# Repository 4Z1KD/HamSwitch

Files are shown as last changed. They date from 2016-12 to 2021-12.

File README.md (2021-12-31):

<meta property="og:image" content="https://raw.githubusercontent.com/4Z1KD/HamSwitch/master/Images/HamSwitch.png" />
<h1>HamSwitch</h1>

<h2>Prototype</h2>
<iframe width="560" height="315" src="https://www.youtube.com/embed/4PVtKeFedng?rel=0" frameborder="0" allow="autoplay; encrypted-media" allowfullscreen></iframe>

<h2>Hardware</h2>
<table>
<tr>
  <td>Arduino<br/>'Uno'</td>
  <td>74HC238 -<br/>3 to 8 Decoder</td>
  <td>Rotary<br/>Encoder</td>
  <td>LCD</td>
  <td>DC Relay<br/>(Array of 8)</td>
</tr>
<tr>
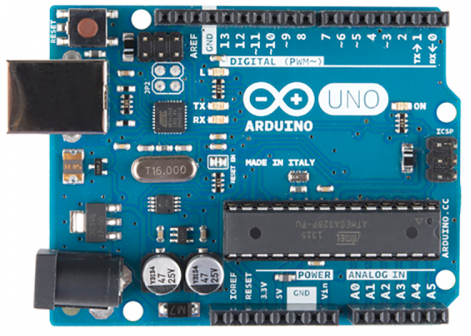
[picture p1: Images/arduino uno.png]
  <td></td>
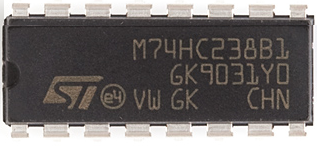
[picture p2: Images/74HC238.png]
  <td></td>
  <td></td>
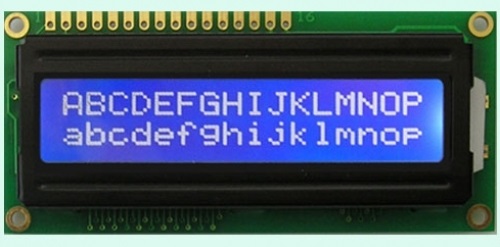
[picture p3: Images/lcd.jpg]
  <td></td>
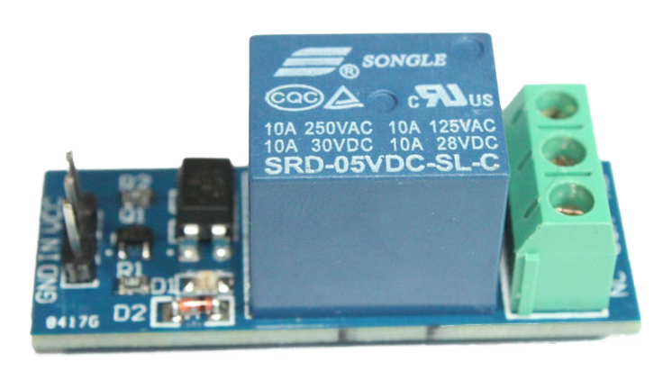
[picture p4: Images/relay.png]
  <td></td>
</tr>
  <tr>
    <td>Resistors</td>
    <td>Diodes</td>
  <td>2n2222<br/>Transistors</td>
    <td>Max232</td>
  </tr>
  <tr>
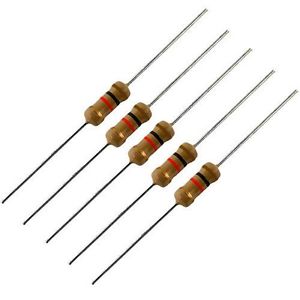
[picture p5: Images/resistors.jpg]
    <td></td>
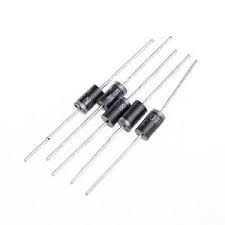
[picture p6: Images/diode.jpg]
    <td></td>
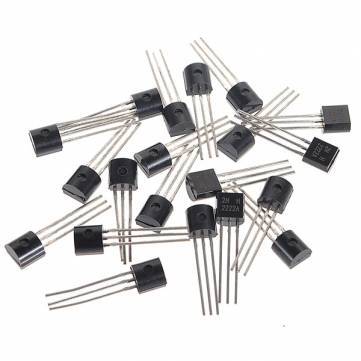
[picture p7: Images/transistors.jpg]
  <td></td>
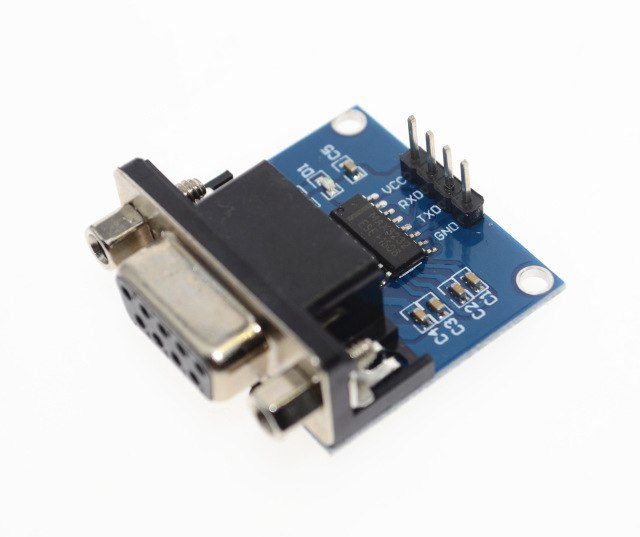
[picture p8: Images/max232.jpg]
    <td></td>
  </tr>
</table>

<h2>Application</h2>
HamSwitch allows the user to toggle between 2 antenna selection modes:<br>
1. Automatic (Radio Priority Mode)<br>
2. Manual (Manual Only Mode)<br>

In "Radio Priority Mode", the 3 to 8 decoder selects the relay (antenna)<br>
based on the frequency input from the radio, while maintaining the user manual selection capability.<br>
if the user turns the rotary encoder, HamSwitch will change back to "Manual only" mode.<br>

In "Manual Only Mode", the radio input is ignored (The controller does not send CAT requests) and the 3 to 8 decoder<br>
selects the relay (antenna) based on the user input from the rotary encoder.<br>

<h3>Emergency Button</h3>
Clicking the rotary encoder button changes to "Manual Only Mode" and selects the dummy load.<br>

<h3>State Persistence</h3>
Every change in the selected antenna and in the selection mode is saved to the eeprom and loaded when HamSwitch is turned on.
This way the user gets his HamSwitch just as it was left..

<h2>Schematics</h2>

Here is the main Schema:<br>
<a href="https://raw.githubusercontent.com/4Z1KD/HamSwitch/master/Images/Main%20Schema.PNG" target="_blank">
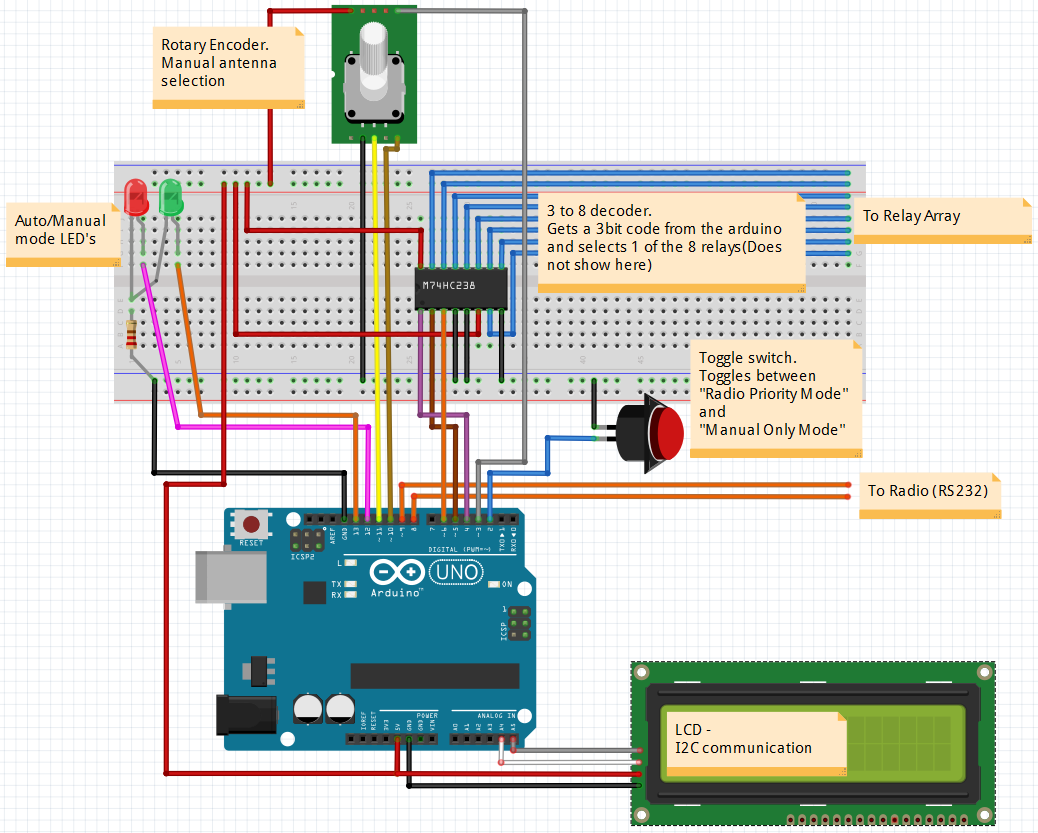
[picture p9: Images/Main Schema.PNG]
HamSwitch Schema

</a>

Here is the Realy Schema:<br>
<a href="https://raw.githubusercontent.com/4Z1KD/HamSwitch/master/Images/Relay%20Schema.PNG" target="_blank">
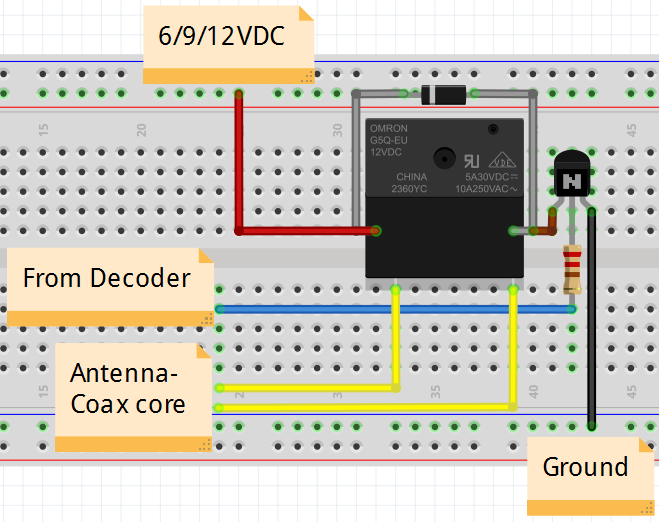
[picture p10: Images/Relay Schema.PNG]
HamSwitch Relay Schema

</a>

<h2>Usage</h2>
All you have to do is to set the radio flag and to populate your list of antennas<br>

<h4>Selecting the radio</h4>
Just open **UserSettings.h** and set *MY_RADIO* to the right value (HamSwitch needs to know which radio you use so it can send the correct commands and correctly parse the response)

```javascript
/*
  ICOM 0
  YAESU 1
  KENWOOD 2
  ELECRAFT 3
*/
const int MY_RADIO = 2;
```
<br/>
You may set the flag AUTO_DETECT_INTERFACE to true and let HamSwitch figure out which interface to use.
```javascript
const bool AUTO_DETECT_INTERFACE = true;
```

<h4>Setting the antenna list</h4>
Antenna has 3 parameters:<br>
**Port** - The Socket number it is connected to. Since HamSwitch supports 8 sockets, this number is in the range of 0-7.<br>
**Bands** - The list of bands it supports.<br>
**Description** - a friendly name e.g. 'Dipole 40'.<br>

If you open **MyAntennaList.h** you'll find a declaration of an array called *AntennaList*.<br>
This is an array of *Antenna* type objects.

```javascript
Antenna* AntennaList[NUM_OF_ANTANNAS];
```

You will also find a method called *InitAntennaList()* and this is the place to define your antennas.<br>
The method is devided to 8 sections - one for each antenna.<br>
The Port is simply the index of the antenna in *AntennaList* array.<br>
Port 0 is **always** the Dummy Load - **Do not change that!**<br>

In order to define the band list, just create a *SimpleList* object.<br>
Use *push_back(int)* to add the band to the list.<br>

Here is an example of how to define a 3 bands (20,15,10) KLM kt-34xa antenna on port 1:<br>

```javascript
SimpleList<int> ant1_BandList;
ant1_BandList.push_back(20);
ant1_BandList.push_back(15);
ant1_BandList.push_back(10);
AntennaList[1] = new Antenna("1", ant1_BandList, "KLM34xa");
```

<h2>License</h2>
**FREE for non commercial use by Amateur Radio Operators**<br>

<h2>Download</h2>
<a href="https://github.com/4Z1KD/HamSwitch/archive/master.zip" target="_blank">Download HamSwitch</a>

<h2>Authors</h2>
Requirements and Analysis: **_Dubi, 4Z5DZ_**<br>
Design and Code: **_Gil, 4Z1KD_**

Latest Version: September 2020<br>
<script>
    var x = document.getElementsByClassName("button");
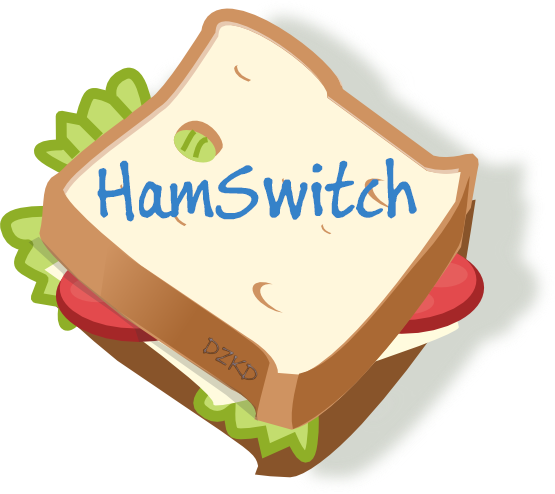
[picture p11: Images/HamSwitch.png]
    x[0].outerHTML = ''
</script>
<style>
.inner
{
  width: 80%;
}
#main-content
{
 width: 80%;
}
#sidebar
{
float:none;
 width: 100%;
}
</style>

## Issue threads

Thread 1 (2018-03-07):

Serial to radio.

runahue, 2018-03-07:
Tnx for your project.
I will try on next days.

Do you connect directly Kenwood RS-232 to Arduino?
Arduino uses 5v and standard serial port (i think) is 12v.
Do you use a max232?

Thank's a lot.

73 de EA5BZ

4Z1KD, 2018-09-17:
Hi Ruben,
I use MAX232 for the interface (Not shown in the diagram)

let me know if you use HamSwitch and send some photos :)
73, Gil 4Z1KD

runahue, 2018-09-18:
Hello Gil.

Yes… i am using it ¡!
I made some modifications.
Now i can use it auto or manual.

Attached some photos.

Thank’s for your work ¡

😊

----------
Ruben Navarro Huedo - EA5BZ
runahue@gmail.com

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

lu6etb, 2021-11-11:
Hi Gil,

Thanks for this project.

Could you please give me more details about how to connect to the radio?
Do you have a diagram?

Thanks
73 de Arturo, LU6ETB

4Z1KD, 2021-11-18:
Hi Arturo,
I am sorry for the late response.
The way to connect HamSwitch to your radio is either directly using the TTL
pins to the radio's CAT input socket or via TTL to RS232 converter.

Which radio do you use?
For instance, I use this method to connect to my FT857D:
[image: image.png]

And my friend uses the other method for his FT991:
[image: image.png]

Let me know if you have any other questions.
73,
Gil 4Z1KD

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

Closed 2021-02-03.

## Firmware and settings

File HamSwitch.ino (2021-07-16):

/**************************************************************************
  # HamSwitch
  <h2>Arduino based auto antenna switch</h2>

  The hardware is based on an Arduino 'Uno' and a 74HC238 - 3 to 8 Line Decoder chip:<br>
  ![Alt text](https://raw.githubusercontent.com/4Z1KD/HamSwitch/master/74HC238.png?raw=true "74HC238 Chip")

  The application allows the user to toggle between 2 antenna selection modes:<br>
  1. Automatic + Manual selection (Radio Priority Mode)<br>
  2. Manual selection (Manual Only Mode)<br>

  In "Radio Priority Mode", the 3 to 8 decoder selects the relay (antenna)<br>
  based on the frequency input from the radio, while maintaining the user manual selection capability.<br>
  if the user turns the rotary encoder, HamSwitch will change back to "Manual only" mode.<br>

  In "Manual Only Mode", the radio input is ignored (The controller does not send CAT requests) and the 3 to 8 decoder<br>
  selects the relay (antenna) based on the user input from the rotary encoder.<br>

  <h3>Emergency Button</h3>
  Clicking the rotary encoder button changes to "Manual Only Mode" and selects the dummy load.<br>

  <h3>State Persistence</h3>
  Every change in the selected antenna and in the selection mode is saved to the eeprom and loaded when HamSwitch is turned on.
  This way the user gets his HamSwitch just as it was left..

  Here is the main Schema:<br>
  <a href="https://raw.githubusercontent.com/4Z1KD/HamSwitch/master/Main%20Schema.PNG" target="_blank">
  ![Alt text](https://raw.githubusercontent.com/4Z1KD/HamSwitch/master/Main%20Schema.PNG?raw=true "HamSwitch Schema")
  </a>

  Here is the Realy Schema:<br>
  <a href="https://raw.githubusercontent.com/4Z1KD/HamSwitch/master/Relay%20Schema.PNG" target="_blank">
  ![Alt text](https://raw.githubusercontent.com/4Z1KD/HamSwitch/master/Relay%20Schema.PNG?raw=true "HamSwitch Relay Schema")
  </a>

**License: This code is FREE for private use by Amateur Radio Operators<br>**
  Created: December 2016<br>
  Last Update: Feb 2021<br>
  Design and Code: **_Gil, 4Z1KD_** (by request from Dubi, 4Z5DZ)<br>
**************************************************************************/

#include <AltSoftSerial.h>
#include <EEPROM.h>
#include "DisplayService.h"
#include "Antenna.h"
#include "MyAntennaList.h"
#include "RadioSettings.h"
#include <LiquidCrystal_I2C.h>
#include <SimpleList.h>

//***************************************************** PIN Definition ***********************************************/

//This is a switch between auto and manual modes
//It is a INPUT_PULLUP pin so by default it is set to 'HIGH'
//In order to change to 'Manual' Mode -> ground this pin temporarily (through toggle switch)
int ToggleModeSwitch_PIN = 2; //Only Pin 2 or Pin 3 allowed here!

//This is an emergency DummyLoad switch
//When pressed, the antenna immediately switches to manual mode and selects the dummy load
int EmergencyDummyLoadSwitch_PIN = 3; //Only Pin 2 or Pin 3 allowed here!

//Define Decoder Pins (for Auto mode)
int Decoder1_PIN_A0 = 6;
int Decoder1_PIN_A1 = 5;
int Decoder1_PIN_A2 = 4;

//Pins 8 and 9 are used as Rx and Tx in AltSoftSerial to communicate with the radio

//Define Rotary Encoder Pins (for Manual mode)
int RotaryEncoder_PIN_CLK = 10;
int RotaryEncoder_PIN_DT = 11;

int AutoMode_RedLED_PIN = 12;
int AutoMode_GreenLED_PIN = 13;

//************************************************** Members *******************************************************/

//Members (This is the place to define variables with global scope used in the application )
AltSoftSerial radioSerial; //a serial port to the radio (pins: 8-RX ,9-TX)
unsigned long Frequency = 0; //The frequency after parsing
unsigned long PreviousFrequency = -1; //The frequency after parsing

bool lastStateCLK = LOW;
bool currentStateCLK = LOW;
bool DT_State = LOW;

int selectedAntenna; //Holds the selected antenna, either in auto or manual mode
int prevSelectedAntenna; //Holds the previously selected antenna - it is used to check if the antenna has changed and print only in this case
bool isManualyAnttenaChanged = false;

//Since we use a physical switch for Auto/Manual mode selection we also need a debounce mechanism
long debouncing_time = 15; //Debouncing Time in Milliseconds
volatile unsigned long last_micros; //in Auto and Manual interrupts
volatile unsigned long emergencyDummyLoad_last_micros; // in emergencyDummyLoad interrupts
volatile unsigned long isr_micros; // in ISR interrupts

volatile bool isModeChanged = true; //Selection Mode change flag - used to display a short message only when the mode changes
volatile bool IsAuto = true; //Auto mode flag

unsigned long previousMillis = 0; // required for delay of CAT command
const long interval = 1000; // delay interval (milliseconds)

LiquidCrystal_I2C lcdx(I2C_ADDR, En_pin, Rw_pin, Rs_pin, D4_pin, D5_pin, D6_pin, D7_pin);
DisplayService dispServe(&lcdx);
Radio myRadio;

//**************************************************************** setup / loop ********************************************************************//
void setup() {
  dispServe.Init();
  InitAntennaList();
  InitRadioList();

  //set Decoder Pin modes
  pinMode(Decoder1_PIN_A0, OUTPUT);
  pinMode(Decoder1_PIN_A1, OUTPUT);
  pinMode(Decoder1_PIN_A2, OUTPUT);

  pinMode(RotaryEncoder_PIN_CLK, INPUT_PULLUP);
  pinMode(RotaryEncoder_PIN_DT, INPUT_PULLUP);

  pinMode(AutoMode_RedLED_PIN, OUTPUT);
  pinMode(AutoMode_GreenLED_PIN, OUTPUT);

  pinMode(ToggleModeSwitch_PIN, INPUT_PULLUP);//Allow automatic switching Pin
  pinMode(EmergencyDummyLoadSwitch_PIN, INPUT_PULLUP);//Emergency Dummy Load Pin - This is the rotary encoder switch

  //Register to interrupts
  attachInterrupt(digitalPinToInterrupt(ToggleModeSwitch_PIN), ToggleMode, FALLING);
  attachInterrupt(digitalPinToInterrupt(EmergencyDummyLoadSwitch_PIN), EmergencyDummyLoad, FALLING);

  //set the interrupt msk
  //PCICR |= (1 << PCIE0);
  //PCMSK0 |= (1 << PCINT2); //Interrupt on pin10
  //PCMSK0 |= (1 << PCINT3); //Interrupt on pin11
  lastStateCLK = digitalRead(RotaryEncoder_PIN_CLK);

  radioSerial.begin(BAUD_RATE);
  Serial.begin(9600); // Open serial communications and wait for port to open:
  while (!Serial) {}
  delay(100);

  if (AUTO_DETECT_INTERFACE)
  {
    myRadio = GetInterface(&radioSerial); //try the different interfaces and select the one for the current radio
    dispServe.Blink(1);
    dispServe.Log11("HamSwitch v2.1", 0, 0, 0, 100);
    dispServe.Log11("Interface: ", 0, 1, 0, 200);
    dispServe.Log11(myRadio.displayname, 11, 1, 0, 250);
  }
  else
  {
    myRadio = GetMyRadio(); //Get a struct that represents a Radio (defined @ RadioSettings.h)
    dispServe.Blink(1);
    dispServe.Log11("HamSwitch v2.1", 0, 0, 0, 100);
    dispServe.Log11("Radio: ", 0, 1, 0, 150);
    dispServe.Log11(myRadio.displayname, 7, 1, 0, 300);
  }

  prevSelectedAntenna = -1; //initialize with out of range value for the first print
  GetFromMemory(); //get the value of the last antenna and the selection mode, before HamSwitch was switched off

  delay(1000);
}

void loop() {
  CheckForData();
  unsigned long currentMillis = millis();
  //----------------------------------------------------------------------------------------------------------//
  //if in auto mode, and it is time to send command (every interval) -> write the command to the radioSerial
  if (IsAuto && (currentMillis - previousMillis >= interval)) {
    previousMillis = currentMillis;
    RadioRequest FrequencyCommandFunction = myRadio.FrequencyCommand; //get the FrequencyCommand from the struct
    if (myRadio.Id != -1) //make sure it is not the DummyRadio
    {
      FrequencyCommandFunction(&radioSerial);
    }
  }
  //----------------------------------------------------------------------------------------------------------//
  //Only alert the user if there was a change in the state
  if (isModeChanged)
  {
    isModeChanged = false; //reset the flag
    SaveModeToMemory(IsAuto);
    if (IsAuto)
    {
      dispServe.Log("Auto Mode", 0, 0, 0); //display a message
      analogWrite(AutoMode_GreenLED_PIN, 0); //Turn green led off
      analogWrite(AutoMode_RedLED_PIN, 130); //Turn red led on
    }
    else
    {
      dispServe.Log("Manual Mode", 0, 0, 0);
      analogWrite(AutoMode_GreenLED_PIN, 130); //Turn green led on
      analogWrite(AutoMode_RedLED_PIN, 0); //Turn red led off
    }
  }
  //----------------------------------------------------------------------------------------------------------//
  //if the antenna was manually changed -> show a short messege
  if (isManualyAnttenaChanged)
  {
    dispServe.Log("Manual Selection", 0, 0, 0);
    isManualyAnttenaChanged = false;
  }
  //----------------------------------------------------------------------------------------------------------//
  //if the entire string has arrived -> parse the frequency and reset the input string
  if (IsAuto) //Auto mode
  {
    if ((Frequency != 0) && (Frequency != PreviousFrequency)) //if the frequency is not 0 (i.e. valid) and has changed -> select the antenna..
    {
      AutoAntennaSelector();
      PreviousFrequency = Frequency;
    }
  }
  //----------------------------------------------------------------------------------------------------------//
  //To prevent flickering, only display the selected antenna if it was a change
  if (prevSelectedAntenna != selectedAntenna)
  {
    DisplaySelectedAntenna(selectedAntenna);
    prevSelectedAntenna = selectedAntenna;
    SwitchTo(selectedAntenna);
    SaveAntennaToMemory(selectedAntenna);
  }
  //----------------------------------------------------------------------------------------------------------//
  updateEncoder();
}


//**************************************************************** Antenna Selection *****************************************************************//
void AutoAntennaSelector()
{
  int band = FrequencyToBand(); //Figure out what is the band equivalent of this frequency
  if (band == 0) //make sure it is on the HAM bands
  {
    dispServe.Log("Non HAM Freq", 0, 0, 0);
    SwitchTo(0);
    return;
  }
  else //if it is
  {
    //iterate over the antenna list
    for (int i = 0; i < NUM_OF_ANTANNAS; i++) {
      SimpleList<int>* mybands = AntennaList[i]->GetBands();
      //and for each antenna, iterate over the bands it supports
      for (SimpleList<int>::iterator itr = mybands->begin(); itr != mybands->end(); ++itr)
      {
        //if you find a match i.e. the antenna supports the selected band
        if (*itr == band)
        {
          dispServe.Log(String(band) + "M   " + String(float(Frequency)/100000, 5), 0, 0, 0); //display the selected band
          SwitchTo(i); //and switch to that antenna
          return;
        }
      }
    }
  }
  dispServe.Log("No ant for " + String(band) + "M", 0, 0, 0);
  SwitchTo(0);
}

//********************************************************************************************************************************************//

//This method gets 3 bits - DecoderA0,DecoderA1, and DecoderA2 and changes the Decoder pins
void SetDecoder1Pins(int DecoderA2, int DecoderA1, int DecoderA0)
{
  (DecoderA0 == 1) ? digitalWrite(Decoder1_PIN_A0, HIGH) : digitalWrite(Decoder1_PIN_A0, LOW);
  (DecoderA1 == 1) ? digitalWrite(Decoder1_PIN_A1, HIGH) : digitalWrite(Decoder1_PIN_A1, LOW);
  (DecoderA2 == 1) ? digitalWrite(Decoder1_PIN_A2, HIGH) : digitalWrite(Decoder1_PIN_A2, LOW);
}

//This method gets the antenna number (0-7) and calls 'SetDecoder1Pins' to change the correct Pins
void SwitchTo(int antenna)
{
  selectedAntenna = antenna;
  switch (antenna)
  {
    case 1:
      SetDecoder1Pins(0, 0, 1);
      break;
    case 2:
      SetDecoder1Pins(0, 1, 0);
      break;
    case 3:
      SetDecoder1Pins(0, 1, 1);
      break;
    case 4:
      SetDecoder1Pins(1, 0, 0);
      break;
    case 5:
      SetDecoder1Pins(1, 0, 1);
      break;
    case 6:
      SetDecoder1Pins(1, 1, 0);
      break;
    case 7:
      SetDecoder1Pins(1, 1, 1);
      break;
    case 0:
      SetDecoder1Pins(0, 0, 0);
      break;
    default:
      SetDecoder1Pins(0, 0, 0);
      break;
  }
}

//********************************************************* Events ***********************************************************************//

void ToggleMode()
{
  static unsigned long last_ToggleModeInterrupt_time = 0;
  unsigned long toggleModeInterrupt_time = millis();
  // If interrupts come faster than 100ms, assume it's a bounce and ignore
  if (toggleModeInterrupt_time - last_ToggleModeInterrupt_time > 500)
  {
    isModeChanged = true;
    IsAuto = !IsAuto;
  }
  last_ToggleModeInterrupt_time = toggleModeInterrupt_time;
}

void EmergencyDummyLoad()
{
  static unsigned long last_EmergencyDummyLoadInterrupt_time = 0;
  unsigned long emergencyDummyLoadInterrupt_time = millis();
  // If interrupts come faster than 100ms, assume it's a bounce and ignore
  if (emergencyDummyLoadInterrupt_time - last_EmergencyDummyLoadInterrupt_time > 500)
  {
    isManualyAnttenaChanged = true;
    isModeChanged = true;
    IsAuto = false;
    Frequency = 0;
    PreviousFrequency = -1;
    SwitchTo(0);
  }
  last_EmergencyDummyLoadInterrupt_time = emergencyDummyLoadInterrupt_time;
}

void  updateEncoder()
{
  currentStateCLK = digitalRead(RotaryEncoder_PIN_CLK);
  if (currentStateCLK != lastStateCLK)
  {
    DT_State = digitalRead(RotaryEncoder_PIN_DT);
    if (DT_State != currentStateCLK)
    {
      selectedAntenna++;
      if (selectedAntenna == NUM_OF_ANTANNAS) selectedAntenna = 0;
    }
    else {
      selectedAntenna--;
      if (selectedAntenna == -1) selectedAntenna = NUM_OF_ANTANNAS-1;
    }
    lastStateCLK = currentStateCLK;
    isManualyAnttenaChanged = true;
    PreviousFrequency = -1;
    isModeChanged = true;
    IsAuto = false;
  }
}

//************************************************* Display ************************************************************************//

void DisplaySelectedAntenna(int antenna)
{
  dispServe.Log(AntennaList[antenna]->GetPort() + ") " + AntennaList[antenna]->GetDescription(), 0, 1, 0);
}

//*************************************************************************************************************************//
void CheckForData() {

  RadioResponse FrequencyResponseFunction = myRadio.FrequencyResponse; //get the FrequencyCommand from the struct
  if (myRadio.Id != -1) //make sure it is not the DummyRadio
  {
    Frequency = FrequencyResponseFunction(&radioSerial);
    //Serial.println(Frequency);
  }
}

void GetFromMemory()
{
  int antenna;
  bool isAuto;
  EEPROM.get( 0, antenna);
  EEPROM.get( sizeof(int), isAuto);
  if (antenna >= 0 && antenna < 8)
  {
    selectedAntenna = antenna;
  }
  IsAuto = isAuto;
}
void SaveAntennaToMemory(int antenna)
{
  EEPROM.put(0, antenna);
}
void SaveModeToMemory(bool isAuto)
{
  EEPROM.put(sizeof(int), isAuto);
}

int FrequencyToBand()
{

  if (Frequency >= 180000 && Frequency <= 200000) {
    return 160;
  }
  else if (Frequency >= 350000 && Frequency <= 400000) {
    return 80;
  }
  else if (Frequency >= 500000 && Frequency <= 550000) {
    return 60;
  }
  else if (Frequency >= 700000 && Frequency <= 730000) {
    return 40;
  }
  else if (Frequency >= 1000000 && Frequency <= 1030000) {
    return 30;
  }
  else if (Frequency >= 1400000 && Frequency <= 1435000) {
    return 20;
  }
  else if (Frequency >= 1800000 && Frequency <= 1817000) {
    return 17;
  }
  else if (Frequency >= 2100000 && Frequency <= 2145000) {
    return 15;
  }
  else if (Frequency >= 2489000 && Frequency <= 2500000) {
    return 12;
  }
  else if (Frequency >= 2800000 && Frequency <= 3000000) {
    return 10;
  }
  else if (Frequency >= 5000000 && Frequency <= 5040000) {
    return 6;
  }
  else if (Frequency >= 7000000 && Frequency <= 7050000) {
    return 4;
  }
  else if (Frequency >= 14400000 && Frequency <= 14600000) {
    return 2;
  }
  else if (Frequency >= 43000000 && Frequency <= 44000000) {
    return 430;
  }
  else {
    return 0;
  }
}

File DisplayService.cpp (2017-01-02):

/*
  DisplayService.cpp - A library for printing text to lcd
  Created by Gil 4Z1KD, December 24, 2016.
*/
#include "Arduino.h"
#include "DisplayService.h"
#include <LiquidCrystal_I2C.h>

DisplayService::DisplayService()
{

}

DisplayService::DisplayService(LiquidCrystal_I2C* lcdx)
{
  //LiquidCrystal_I2C m_lcd(I2C_ADDR, En_pin, Rw_pin, Rs_pin, D4_pin, D5_pin, D6_pin, D7_pin);
  m_lcd = lcdx;
}

void DisplayService::Init()
{
  m_lcd->begin(16, 2);
  m_lcd->setBacklightPin(BACKLIGHT_PIN, POSITIVE);
  m_lcd->setBacklight(HIGH);
  m_lcd->home();
}

void DisplayService::Log(String str, int col, int row, boolean isToClear)
{
  if (isToClear)
    m_lcd->clear();
  m_lcd->setCursor(col, row);
  m_lcd->print("                ");
  m_lcd->setCursor(col, row);
  m_lcd->print(str);
}

void DisplayService::Log11(String str, int col, int row, boolean isToClear, int t_delay)
{
  if (isToClear)
    m_lcd->clear();
  m_lcd->setCursor(col, row);
  char buf[str.length() + 1];
  str.toCharArray(buf, str.length() + 1);
  for (int i = 0; i < str.length(); i++)
  {
    m_lcd->print(buf[i]);
    delay(t_delay);
  }
}

void DisplayService::Blink(int repeats)
{
  for (int i = 0; i < repeats; i++)
  {
    m_lcd->backlight();
    delay(250);
    m_lcd->noBacklight();
    delay(250);
  }
  m_lcd->backlight();
}

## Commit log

2016-12-23 Save and load from memory
    every change in the selected antenna and in the selection mode is saved to memory and loaded when HamSwitch is turned on.
    this way the user gets his HamSwitch as it was left..
2016-12-27 Fritzing library
    [ArduinoAntennaSwitch - Relay.fzz, ArduinoAntennaSwitch.fzz]
2016-12-27 Antenna band list is now SimpleList not int[]
2016-12-27 The antenna list is now a member not a class
2016-12-28 Update Main Schema
    [ArduinoAntennaSwitch.fzz]
2020-09-12 Limit to 14 rigs for arduino nano
2021-02-03 non-interrupt rotary encoder handler
2021-07-15 fix antenna encoder selection for less than 7 antennas
    [HamSwitch.ino]
